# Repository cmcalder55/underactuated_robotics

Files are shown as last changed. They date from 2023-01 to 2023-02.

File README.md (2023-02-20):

# Underactuated Robotic Gripper
Underactuated robotic gripper research performed through the Advanced Robot Manipulators Laboratory at Stevens Institute of Technology under the guidance of Dr. Long Wang in collaboration with lab members. View the lab webpage here: https://longwang.in/

## Background  
This project was focused on creating a low-cost robotic hand that can be attached to a commercial robotic arm for various complex manipulation tasks. The main feature of the design is the underactuation system, meaning multiple joints can be controlled by one mechanism. Inspired by human biology, underactuation can be used to create self-adaptive mechanisms, such as in DaVinci's wing design seen below [(source)](https://en.wikipedia.org/wiki/Self-adaptive_mechanisms/). 

<p align="center">
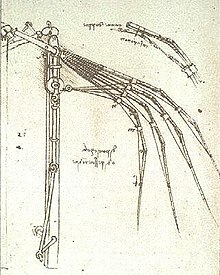
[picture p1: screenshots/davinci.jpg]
Da Vinci's self-adaptive flapping wings.
  
</p>

For robotic gripper designed in this project, tendon-driven underactuation is used to control 8 finger joints using only 2 motors. The manipulator can be positioned and commanded directly by a user. The manipulator uses force and angle sensors to optimize its grasp. Tasks can also be performed autonomously using sensor feedback.  

## Simulation
First, a SolidWorks model of the robotic hand was created. Once the model was approved, a physical prototype was created and attached to a Kinova robotic arm. **Watch the physical prototype in motion [here](https://youtube.com/shorts/SLhP_C6LJS4?feature=share/).**  

<p align="center">
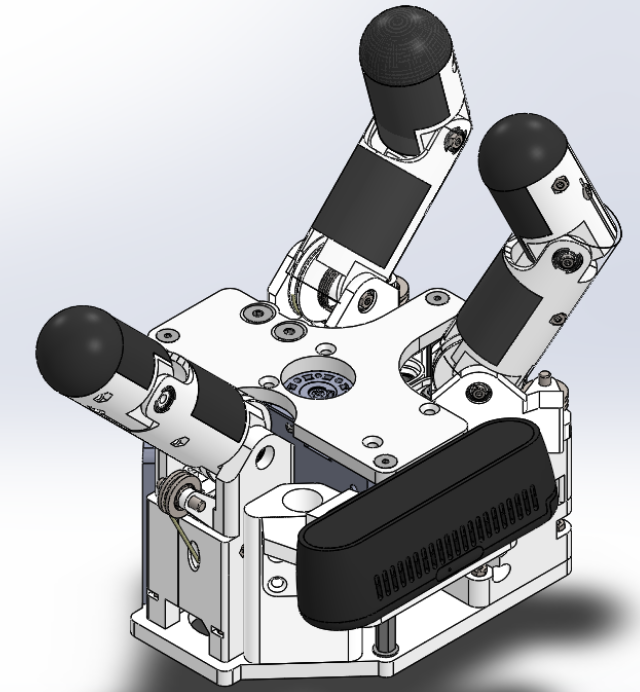
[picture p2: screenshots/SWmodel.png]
SolidWorks 3D model.
  
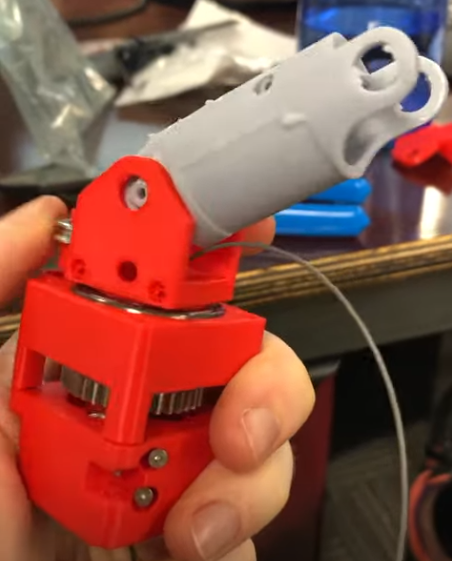
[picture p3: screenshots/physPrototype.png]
Physical prototyping.
  
</p>

The SolidWorks model was then converted to a URDF (Unified Robot Description Format). The URDF model was loaded into the robot simulator program Gazebo and attached to a Kinova arm model (available on their website). For initial testing, a model of a soda can was used as the target. ROS code was written to define each link and joint of the system. Through a RViz controller GUI, the inertia of each joint can be adjusted using a slider or direct inputs.   

<p align="center">
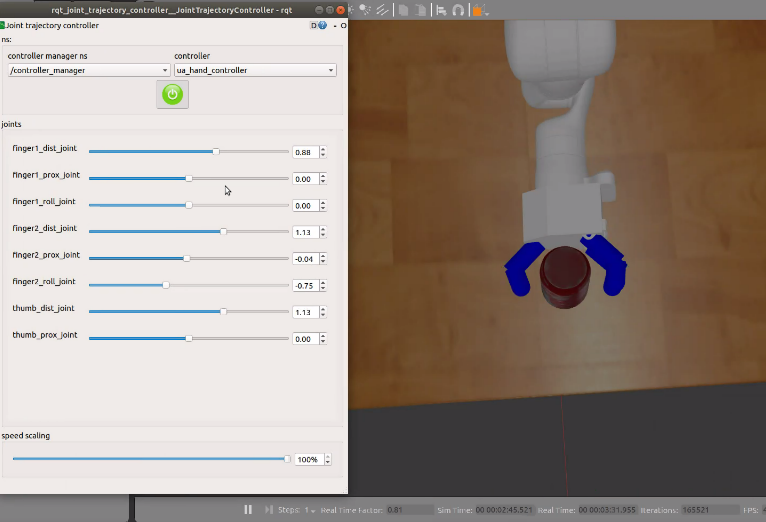
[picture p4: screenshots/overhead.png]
Target gripping overhead view.
  
</p>

After choosing the desired end position, a path planning algorithm is used to find the shortest and smoothest path. After the gripper is positioned, it tightens around the object until it receives sufficient force feedback to try and pick up the object. The joint positions and inertias can then be adjusted to optimize its path and grip strength. 
**See the can being lifted [here](https://youtu.be/HWir0G_nYKU/).**    

<p align="center">
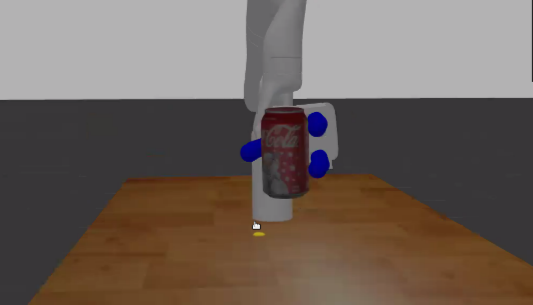
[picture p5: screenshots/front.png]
Target lifting front view.
  
</p> 

When the robot was able to successfully pick up the can, further tests were run using a cube and a door handle. This was done to ensure the robot could adjust to a variety of target geometries and angles. This also helped to ensure the simulation modeled the physical sensors correctly, since the manipulation task could also be run in real time with the same commands on the physical system.

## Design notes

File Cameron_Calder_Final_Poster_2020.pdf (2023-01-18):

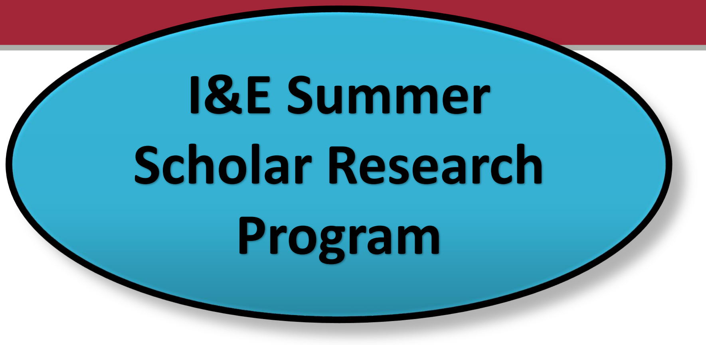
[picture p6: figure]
I&E Summer Scholar Research Program

## Simulations of a Highly Underactuated Robotic Hand

Cameron Calder, Dr. Long Wang, Dept. of Mechanical Engineering

## hello Robotic Hands and Grippers

Robotic hands and grippers dominating the
market today are fully actuated, meaning each
joint is directly controllable.
- Increases complexity
- Very expensive
- Used widely in manufacturing

# IP Potential

I&E Summer Scholar
Poster Conference

# Commercial Application

## Research Description

- Development and simulation of a robotic hand with a highly underactuated design
- 8 moving joints, 2 motors
- Opening/closing
- spreading apart

## Research Methods

## Results & Conclusions

- Through these simulations, this design was able to pick up objects through user teleop control
- Shows strength of the gripper, application, and potential for customization to fit the consumer’s field
- Working on a script for autonomous object manipulation

# Commercial Application

- The robotic hand/gripper market was valued at $1.2 billion in 2019 and a CAGR of 10% 2019-29
- Can be end effectors for a variety of systems
- This design is 5-10x cheaper than current models dominating the market
- Tendon-driven joint
movement
.STL model | Physical prototyping
Direct joint control | Autonomous manipulation

The software accompanying this design to perform and automate manipulation tasks could be licensed. Novel designs are being prototyped for this hand but is not the research’s focus due to COVID-19.

1 | 2
3 | 4

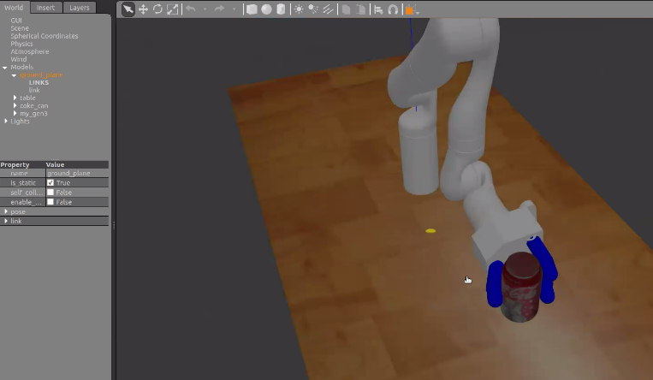
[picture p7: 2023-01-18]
screenshots/side.png

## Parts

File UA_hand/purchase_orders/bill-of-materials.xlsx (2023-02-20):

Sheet: palm_subasm
Sub-asm | ITEM NO. | PART NUMBER | DESCRIPTION | QTY. | Vender | Added to Cart | Cart line number | Received
Palm | 1 | palm_base |  | 1 | laser cutting
Palm | 2 | palm_top_plate |  | 1 | laser cutting
Palm | 3 | 91115A155 |  | 3 | McMaster | NASA-V3.15-MCM-1 | 1
Palm | 4 | 90965A130 |  | 3 | McMaster | NASA-V3.15-MCM-1 | 2
Palm | 5 | 91253A108 |  | 6 | McMaster | NASA-V3.15-MCM-1 | 3
Palm | 6 | main-pulley-support- module^palm_subas m |  | 1 | subasm
Palm | 6.1 | bearing_support_asm |  | 1 | subasm
Palm | 6.1.1 | bearing_support_ |  | 1 | 3D print
Palm | 6.1.2 | 7804K115 |  | 1 | McMaster | NASA-V3.15-MCM-1 | 4
Palm | 6.2 | 92125A056 |  | 2 | McMaster | NASA-V3.15-MCM-1 | 5
Palm | 7 | AX_12A_pulley_asm |  | 1 | Dynamixel
Palm | 7.1 | AX-12A |  | 1 | Dynamixel
Palm | 7.1.1 | AX-12A-01 |  | 1 | Dynamixel
Palm | 7.1.2 | AX-12A-02 |  | 1 | Dynamixel
Palm | 7.1.3 | AX-12A-03 |  | 1 | Dynamixel
Palm | 7.1.4 | AX-12A-04 |  | 1 | Dynamixel
Palm | 7.1.5 | SetScrew |  | 4 | Dynamixel
Palm | 7.2 | servo_pulley_ |  | 1 | 3D print
Palm | 8 | XL-320-gear |  | 1 | Dynamixel
Palm | 8.1 | XL-320 |  | 1 | Dynamixel
Palm | 8.2 | XL-320-hub |  | 1 | 3D print
Palm | 8.3 | a 1t 2-y32024 | roll motor gear, plastic | 1 | SDP/SI
Palm | 8.3 copy | 7880K31 | roll motor gear, metal replacement on McMaster | 1 | McMaster | NASA-V3.15-MCM-1 | 6
Palm | 8.3 copy-A | 92015A103 | set screw needed | 5 | McMaster | NASA-V3.15-MCM-1 | 7
Palm | 8.4 | 91698A200 |  | 4 | McMaster | NASA-V3.15-MCM-2 | 3
Palm | 8.5 | 90940A411 |  | 4 | McMaster | NASA-V3.15-MCM-2 | 2
Palm | 8.6 | 97395A471 |  | 1 | McMaster | NASA-V3.15-MCM-2 | 1
Palm | 9 | 91292A832 |  | 5 | McMaster | NASA-V3.15-MCM-1 | 8
Palm | 10 | 90710A020 |  | 5 | McMaster | NASA-V3.15-MCM-1 | 9
Palm | 11 | 92095A199 |  | 2 | McMaster | NASA-V3.15-MCM-1 | 10
Palm | 12 | 91854A101 |  | 2 | McMaster | NASA-V3.15-MCM-1 | 11
Palm | 13 | roll-motor-idler- module^palm_subasm |  | 1 | subasm | Palm-Cart
Palm | 13.1 | bearing_support_asm |  | 1 | subasm | Palm-Cart
Palm | 13.1.1 | bearing_support_ |  | 1 | 3D print
Palm | 13.1.2 | 7804K115 |  | 1 | McMaster | NASA-V3.15-MCM-1 | 12
Palm | 13.2 | a 1m 2-ta32032 | roll_motor_idler | 1 | SDP/SI
Palm | 13.2 copy | 6832K54 | replacement of the plastic version on SDP/SI | 1 | McMaster | NASA-V3.15-MCM-1 | 54
Palm | 13.3 | roll_motor_idler_stando ff |  | 2 | 3D print
Palm | 13.4 | 93395A150 |  | 2 | McMaster | NASA-V3.15-MCM-1 | 13
 | 13.5 | roll_motor_idler_step_s haft |  | 1 | 3D print

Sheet: thumb_subasm
Sub-asm | ITEM NO. | PART NUMBER | QTY. | Vender | Added to Cart | Cart line number | Received
Thumb | 1 | thumb-base- subasm^thumb_subas m | 1 | subasm
Thumb | 1.1 | thumb_base | 1 | 3D print
Thumb | 1.2 | 7804K104 | 2 | McMaster | NASA-V3.15-MCM-1 | 14
Thumb | 1.3 | guiding_pulley_asm | 1 | subasm
Thumb | 1.3.1 | palm_pulley_support | 1 | 3D print
Thumb | 1.3.2 | 3434T21 | 1 | McMaster | NASA-V3.15-MCM-1 | 15
Thumb | 1.3.3 | 98105A085 | 1 | McMaster | NASA-V3.15-MCM-1 | 16
Thumb | 1.3.4 | 93395A150 | 2 | McMaster | NASA-V3.15-MCM-1 | 17
Thumb | 1.3.5 | 91828A111 | 2 | McMaster | NASA-V3.15-MCM-1 | 18
Thumb | 1.4 | 93395A150 | 4 | McMaster | NASA-V3.15-MCM-1 | 19
Thumb | 1.5 | 90591A265 | 6 | McMaster | NASA-V3.15-MCM-1 | 20
Thumb | 1.6 | 98105A085 | 1 | McMaster | NASA-V3.15-MCM-1 | 21
Thumb | 1.7 | 3434T21 | 1 | McMaster | NASA-V3.15-MCM-1 | 22
Thumb | 1.8 | thumb_tendon_routing | 1 | N/A
Thumb | 1.9 | 91292A034 | 2 | McMaster | NASA-V3.15-MCM-1 | 23
Thumb | 2 | thumb-prox- subasm^thumb_subas m | 1 | subasm
Thumb | 2.1 | thumb_prox_link | 1 | 3D print
Thumb | 2.2 | thumb_prox_pulley | 1 | 3D print
Thumb | 2.3 | thumb_prox_rubber | 1 | 3D print
Thumb | 2.4 | thumb_prox_bushing | 1 | 3D print
Thumb | 2.5 | 7804K104 | 1 | McMaster | NASA-V3.15-MCM-1 | 24
Thumb | 2.6 | 7804K104 | 2 | McMaster | NASA-V3.15-MCM-1 | 25
Thumb | 3 | thumb-tip- subasm^thumb_subas m | 1 | subasm
Thumb | 3.1 | thumb_dist_link | 1 | 3D print
Thumb | 3.2 | thumb_dist_rubber | 1 | 3D print
Thumb | 3.3 | thumb_fingertip | 1 | 3D print

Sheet: finger_subasm
Sub-asm | ITEM NO. | PART NUMBER | DESCRIPTION | QTY. | Vender | Added to Cart | Cart line number | Received | Multiple copies | Total QTY.
Finger | 1 | finger-base- module^finger_subas m_pulley |  | 1 | subasm |  |  |  | 2 | 2
Finger | 1.1 | finger_base_ |  | 1 | 3D print |  |  |  | 2 | 2
Finger | 1.2 | finger_base_extend |  | 1 | 3D print |  |  |  | 2 | 2
Finger | 1.3 | 5972K157 |  | 1 | McMaster | NASA-V3.15-MCM-1 | 26 |  | 2 | 2
Finger | 1.4 | guiding_pulley_asm |  | 1 | subasm |  |  |  | 2 | 2
Finger | 1.4.1 | palm_pulley_support |  | 1 | 3D print |  |  |  | 2 | 2
Finger | 1.4.2 | 3434T21 |  | 1 | McMaster | NASA-V3.15-MCM-1 | 27 |  | 2 | 2
Finger | 1.4.3 | 98105A085 |  | 1 | McMaster | NASA-V3.15-MCM-1 | 28 |  | 2 | 2
Finger | 1.4.4 | 93395A150 |  | 2 | McMaster | NASA-V3.15-MCM-1 | 29 |  | 2 | 4
Finger | 1.4.5 | 91828A111 |  | 2 | McMaster | NASA-V3.15-MCM-1 | 30 |  | 2 | 4
Finger | 1.5 | finger_tendon_routing _lower |  | 1 | N/A |  |  |  | 2 | 2
Finger | 1.6 | 93395A150 |  | 3 | McMaster | NASA-V3.15-MCM-1 | 31 |  | 2 | 6
Finger | 1.7 | 90591A265 |  | 7 | McMaster | NASA-V3.15-MCM-1 | 32 |  | 2 | 14
Finger | 1.8 | 91292A032 |  | 4 | McMaster | NASA-V3.15-MCM-1 | 33 |  | 2 | 8
Finger | 1.9 | 57155K16 |  | 2 | McMaster | NASA-V3.15-MCM-1 | 34 |  | 2 | 4
Finger | 2 | finger-roll- module^finger_subas m_pulley |  | 1 | subasm |  |  |  | 2 | 2
Finger | 2.1 | finger_roll_base |  | 1 | 3D print |  |  |  | 2 | 2
Finger | 2.2 | 98105A085 |  | 1 | McMaster | NASA-V3.15-MCM-1 | 35 |  | 2 | 2
Finger | 2.3 | 3434T21 |  | 1 | McMaster | NASA-V3.15-MCM-1 | 36 |  | 2 | 2
Finger | 2.4 | horizontal-shaft- pulley^finger-roll- module_finger_subas m_pulley |  | 1 | subasm |  |  |  | 2 | 2
Finger | 2.4.1 | 57155K381 |  | 1 | McMaster | NASA-V3.15-MCM-1 | 37 |  | 2 | 2
Finger | 2.4.2 | 98105A081 |  | 1 | McMaster | NASA-V3.15-MCM-1 | 38 |  | 2 | 2
Finger | 2.4.3 | finger_shaft_pulley_cus tom |  | 1 | 3D print |  |  |  | 2 | 2
Finger | 2.5 | 7804K104 |  | 2 | McMaster | NASA-V3.15-MCM-1 | 39 |  | 2 | 4
Finger | 2.6 | finger_tendon_routing |  | 1 | N/A |  |  |  | 2 | 2
Finger | 2.7 | 91292A032 |  | 2 | McMaster | NASA-V3.15-MCM-1 | 40 |  | 2 | 4
Finger | 2.8 | 90591A265 |  | 2 | McMaster | NASA-V3.15-MCM-1 | 41 |  | 2 | 4
Finger | 2.9 | 6832K55 |  | 1 | McMaster | NASA-V3.15-MCM-1 | 42 |  | 2 | 2
Finger | 3 | finger-prox- module^finger_subas m_pulley |  | 1 | subasm |  |  |  | 2 | 2
Finger | 3.1 | finger_prox_link |  | 1 | 3D print |  |  |  | 2 | 2
Finger | 3.2 | 7804K104 |  | 3 | McMaster | NASA-V3.15-MCM-1 | 43 |  | 2 | 6
Finger | 3.3 | finger_prox_bushing |  | 1 | 3D print |  |  |  | 2 | 2
Finger | 3.4 | finger_prox_pulley |  | 1 | 3D print |  |  |  | 2 | 2
Finger | 3.5 | finger_prox_rubber |  | 1 | N/A |  |  |  | 2 | 2
Finger | 3.6 | 91292A032 |  | 1 | McMaster | NASA-V3.15-MCM-1 | 44 |  | 2 | 2
Finger | 3.7 | 90591A265 |  | 2 | McMaster | NASA-V3.15-MCM-1 | 45 |  | 2 | 4
Finger | 3.8 | 91292A002 |  | 1 | McMaster | NASA-V3.15-MCM-1 | 46 |  | 2 | 2
Finger | 4 | finger-tip- module^finger_subas m_pulley |  | 1 | subasm |  |  |  | 2 | 2
Finger | 4.1 | finger_dist_link |  | 1 | 3D print |  |  |  | 2 | 2
Finger | 4.2 | finger_dist_rubber |  | 1 | 3D print |  |  |  | 2 | 2
Finger | 4.3 | finger_fingertip |  | 1 | 3D print |  |  |  | 2 | 2
Finger | 4.4 | 92290A013 |  | 1 | McMaster | NASA-V3.15-MCM-1 | 47 |  | 2 | 2
Finger | 4.5 | 90591A265 |  | 3 | McMaster | NASA-V3.15-MCM-1 | 48 |  | 2 | 6
Finger | 4.6 | 91292A002 |  | 1 | McMaster | NASA-V3.15-MCM-1 | 49 |  | 2 | 2
Finger | 4.7 | 91292A032 |  | 1 | McMaster | NASA-V3.15-MCM-1 | 50 |  | 2 | 2

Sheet: rolling_idler_subasm
Sub-asm | ITEM NO. | PART NUMBER | DESCRIPTION | QTY. | Vender | Added to Cart | Cart line number | Received | Multiple copies | Total QTY.
Rolling_idler | 1 | 7880K29 |  | 1 | McMaster | NASA-V3.15-MCM-1 | 51 |  | 2 | 2
Rolling_idler | 2 | 90730A009 |  | 1 | McMaster | NASA-V3.15-MCM-1 | 52 |  | 2 | 2
Rolling_idler | 3 | 92952A230 |  | 1 | McMaster | NASA-V3.15-MCM-1 | 53 |  | 2 | 2
Rolling_idler | 4 | roll_idler_spacer |  | 1 | 3D print |  |  |  | 2 | 2

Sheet: General
Sub-asm | ITEM NO. | PART NUMBER | DESCRIPTION | QTY. | Vender | Added to Cart | Cart line number | Received
General | 1 | 014725M | Stanley 014725 25-Removable Compartment Professional Organizer | 2 | Amazon

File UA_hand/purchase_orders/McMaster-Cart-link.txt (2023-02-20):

https://www.mcmaster.com/order/rcvRtedOrd.aspx?ordid=4893269417478&lnktyp=txt

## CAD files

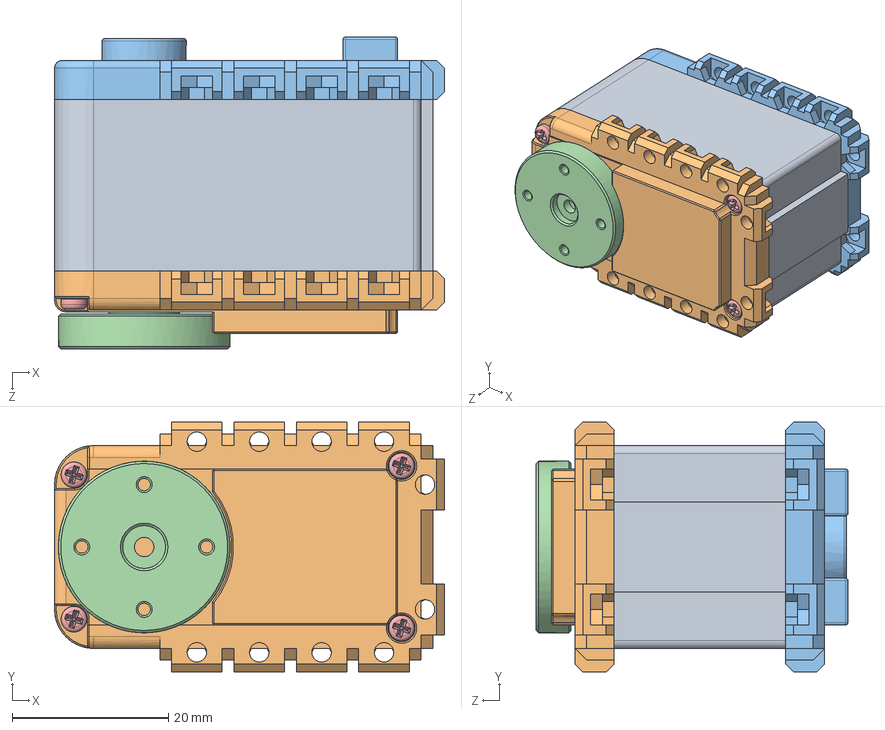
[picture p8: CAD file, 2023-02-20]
UA_hand/wanglong06-data-nasa-hand-cad-23e008917a00/AX-12A/AX-12A.SLDASM
50.0 x 32.0 x 40.0 mm
AX-12A-01
AX-12A-02
AX-12A-03
AX-12A-04
SetScrew x 4

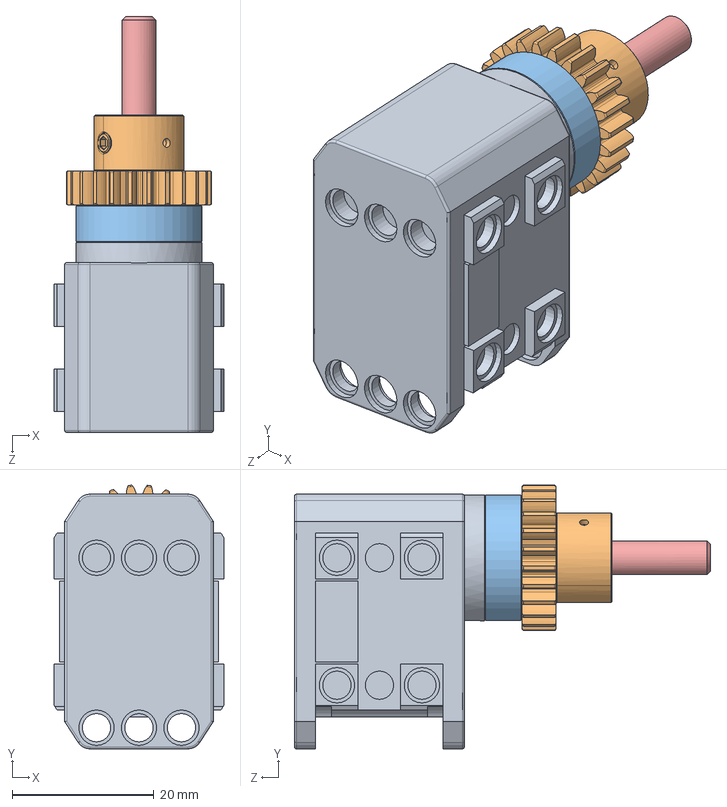
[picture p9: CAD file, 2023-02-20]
UA_hand/XL-320/XL-320-gear.sldasm
24.0 x 37.3 x 58.8 mm
XL-320
roll_motor_gear_a_1t_2-y32024
XL-320-hub
xl-320-mount-m2x4-91698A200 x 4
xl-320-gear-pin-90145A512

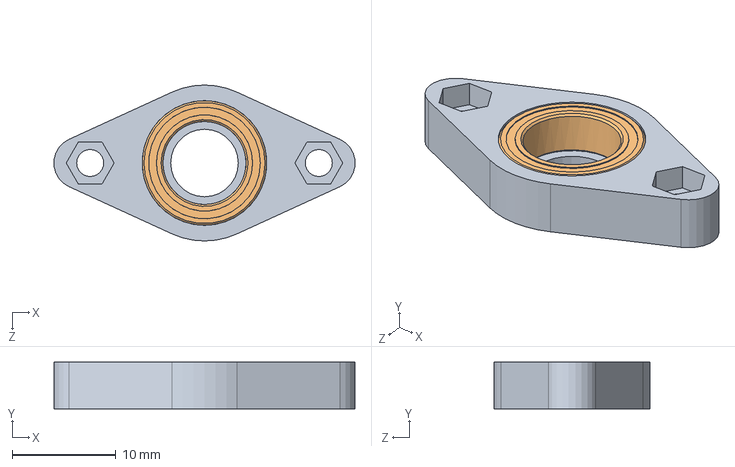
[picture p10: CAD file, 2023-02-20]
UA_hand/wanglong06-data-nasa-hand-cad-23e008917a00/AX-12A/bearing_support_asm.SLDASM
29.0 x 4.50 x 15.0 mm
bearing_support_
servo_pulley_bearing_7804K115_STAINLESS STEEL BALL BEARING

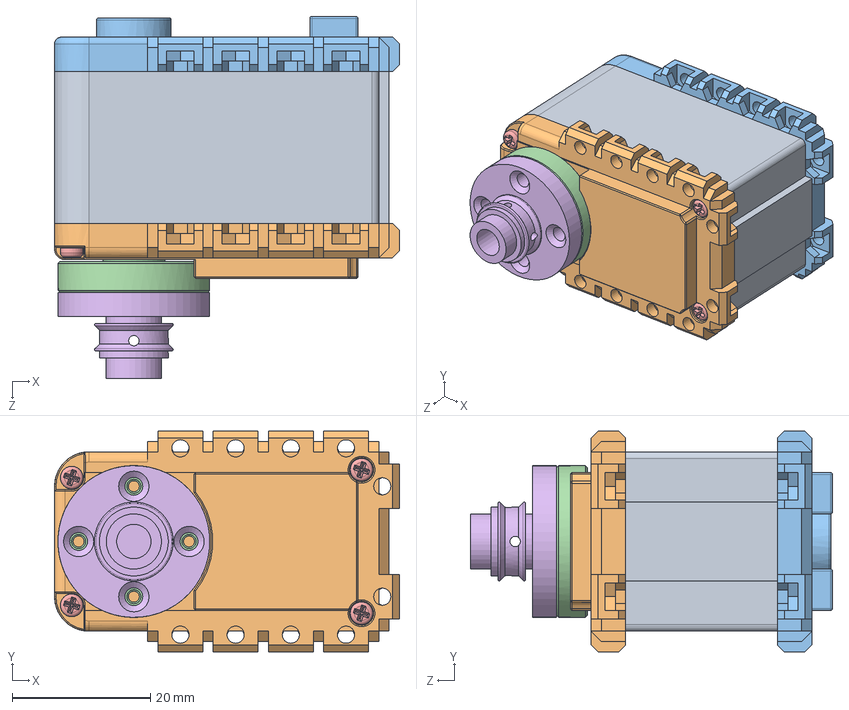
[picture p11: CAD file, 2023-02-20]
UA_hand/AX-12A/AX_12A_pulley_asm.SLDASM
50.0 x 32.0 x 52.5 mm
AX-12A-01
AX-12A-02
AX-12A-03
AX-12A-04
SetScrew x 4
servo_pulley_

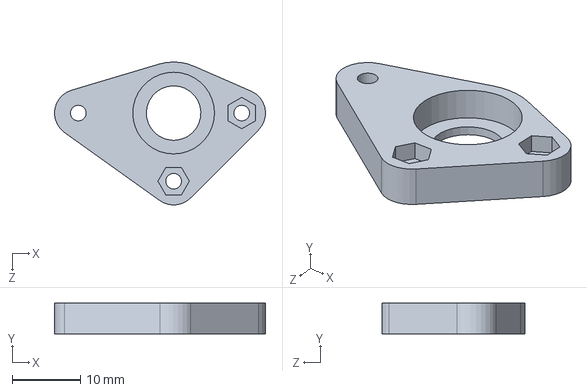
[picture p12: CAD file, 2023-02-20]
UA_hand/AX-12A/bearing_support_3_legs.SLDPRT
31.0 x 4.50 x 21.0 mm

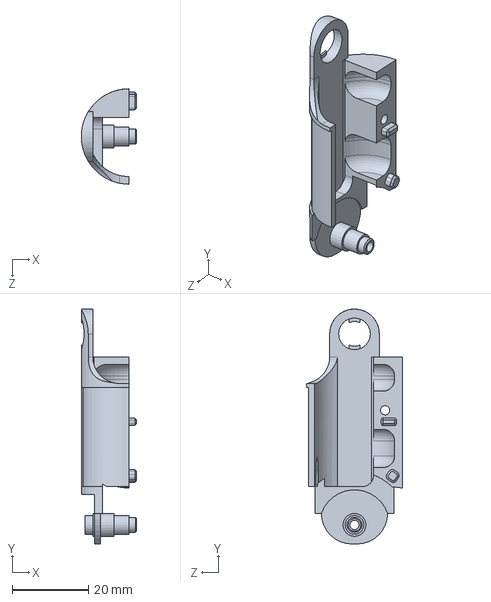
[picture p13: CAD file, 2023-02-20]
UA_hand/finger_subasm/finger_prox_link-split-b.SLDPRT
14.5 x 61.5 x 25.0 mm

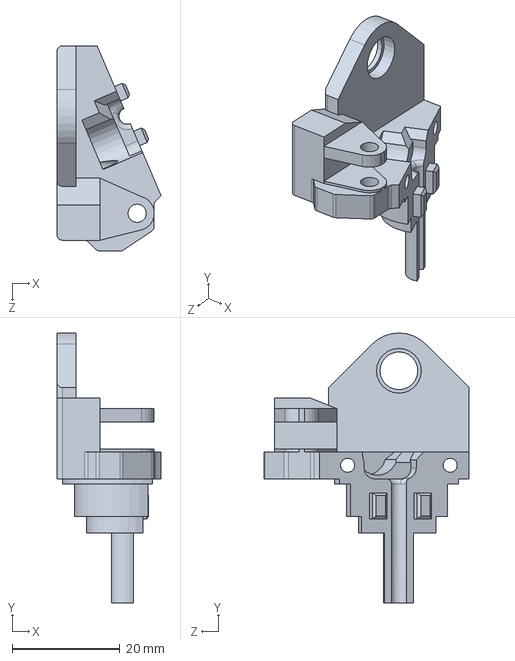
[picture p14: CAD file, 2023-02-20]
UA_hand/mir-finger_subasm/mir-finger_roll_base-finger_roll_base-split-a.SLDPRT
19.3 x 50.0 x 38.0 mm

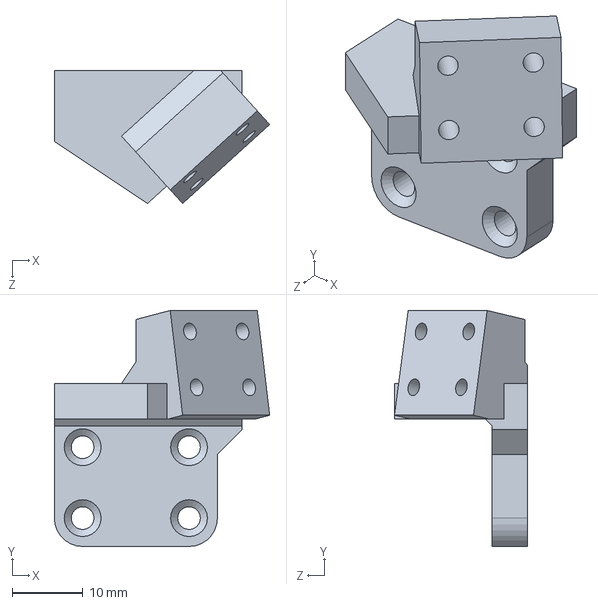
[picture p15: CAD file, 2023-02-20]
UA_hand/palm_subasm/IntelRealsense_connector.SLDPRT
30.4 x 33.3 x 18.8 mm

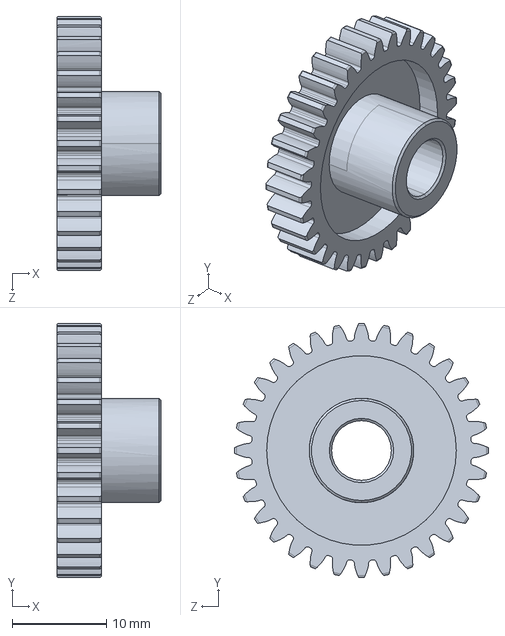
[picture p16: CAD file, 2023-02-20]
UA_hand/roll_gears/roll_motor_idler_a_1m_2-ta32032.SLDPRT
11.1 x 27.0 x 27.0 mm

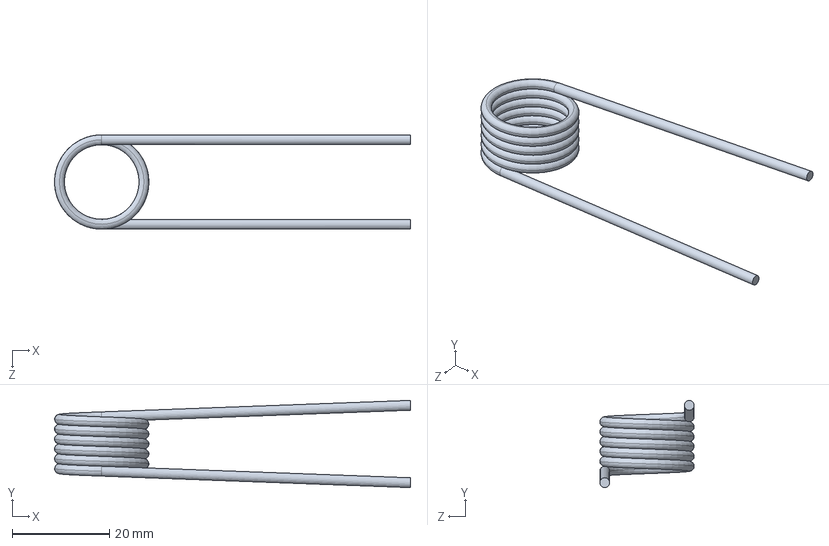
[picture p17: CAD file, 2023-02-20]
UA_hand/Spring/spring_dist_thumb_LTL021D08M.SLDPRT
73.2 x 17.9 x 19.4 mm

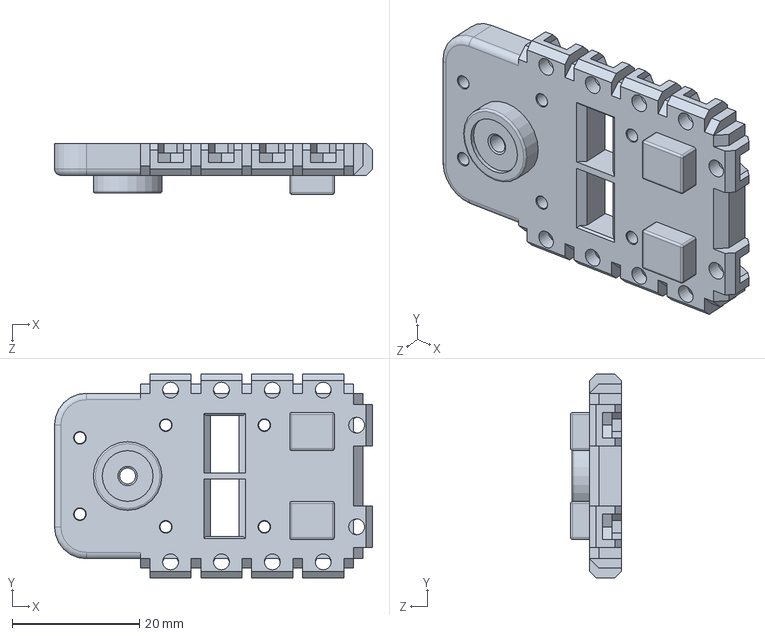
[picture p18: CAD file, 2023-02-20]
UA_hand/wanglong06-data-nasa-hand-cad-23e008917a00/AX-12A/AX-12A-03.SLDPRT
50.0 x 32.0 x 8.00 mm

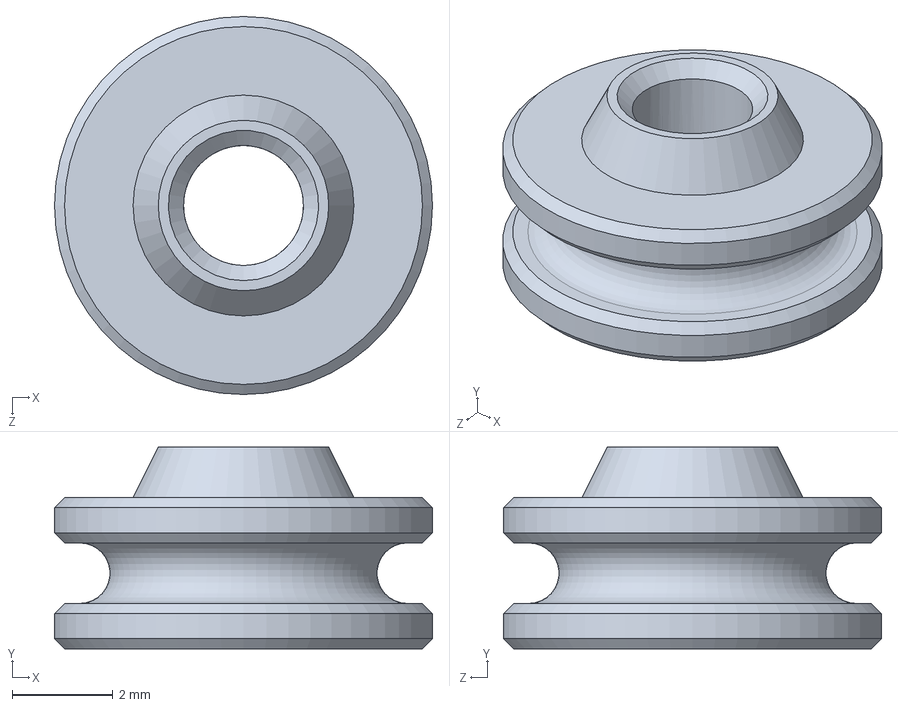
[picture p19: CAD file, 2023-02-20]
UA_hand/wanglong06-data-nasa-hand-cad-23e008917a00/finger_subasm/finger_shaft_pulley_custom.SLDPRT
7.50 x 4.00 x 7.50 mm

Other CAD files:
UA_hand/mir-finger_subasm/mir-guiding_pulley_asm.SLDASM
UA_hand/wanglong06-data-nasa-hand-cad-23e008917a00/mir-finger_subasm/mir-guiding_pulley_asm.SLDASM
UA_hand/AX-12A/AX-12A-01.SLDPRT
UA_hand/AX-12A/AX-12A-02.SLDPRT
UA_hand/AX-12A/AX-12A-04.SLDPRT
UA_hand/AX-12A/SetScrew.SLDPRT
UA_hand/AX-12A/bearing_support.SLDPRT
UA_hand/AX-12A/bearing_support_.SLDPRT
UA_hand/AX-12A/roll_motor_support_hub.SLDPRT
UA_hand/AX-12A/screw_bearing_support_92125A056.SLDPRT
UA_hand/AX-12A/screw_servo_pulley_93395A138.SLDPRT
UA_hand/AX-12A/servo_pulley_.SLDPRT
UA_hand/AX-12A/servo_pulley_bearing_7804K104.SLDPRT
UA_hand/AX-12A/servo_pulley_bearing_7804K115_STAINLESS STEEL BALL BEARING.SLDPRT
UA_hand/Spring/spring_prox_finger_LTML100T06M.SLDPRT
UA_hand/XL-320/XL-320-hub.SLDDRW
UA_hand/XL-320/XL-320-hub.SLDPRT
UA_hand/XL-320/XL-320.SLDPRT
UA_hand/XL-320/roll_motor_gear_a_1t_2-y32024.SLDPRT
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
